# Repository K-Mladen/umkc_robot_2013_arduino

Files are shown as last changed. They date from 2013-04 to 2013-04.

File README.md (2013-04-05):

umkc_robot_2013_arduino
=======================

This is the Arduino code for the UMKC Robotics Team for the 2013 IEEE R5 
competition.

Flash this to the Arduino using the Arduino IDE version 0023. (NOT any 
version above 1.0)

Include the ros_lib directory in Arduino's libraries, either in it's own 
directory\libraries, or under your Documents\Arduino\libraries

Wiring diagram included in PDF and FZZ (Fritzing) format. Frizing is available
by going to www.fritzing.org.

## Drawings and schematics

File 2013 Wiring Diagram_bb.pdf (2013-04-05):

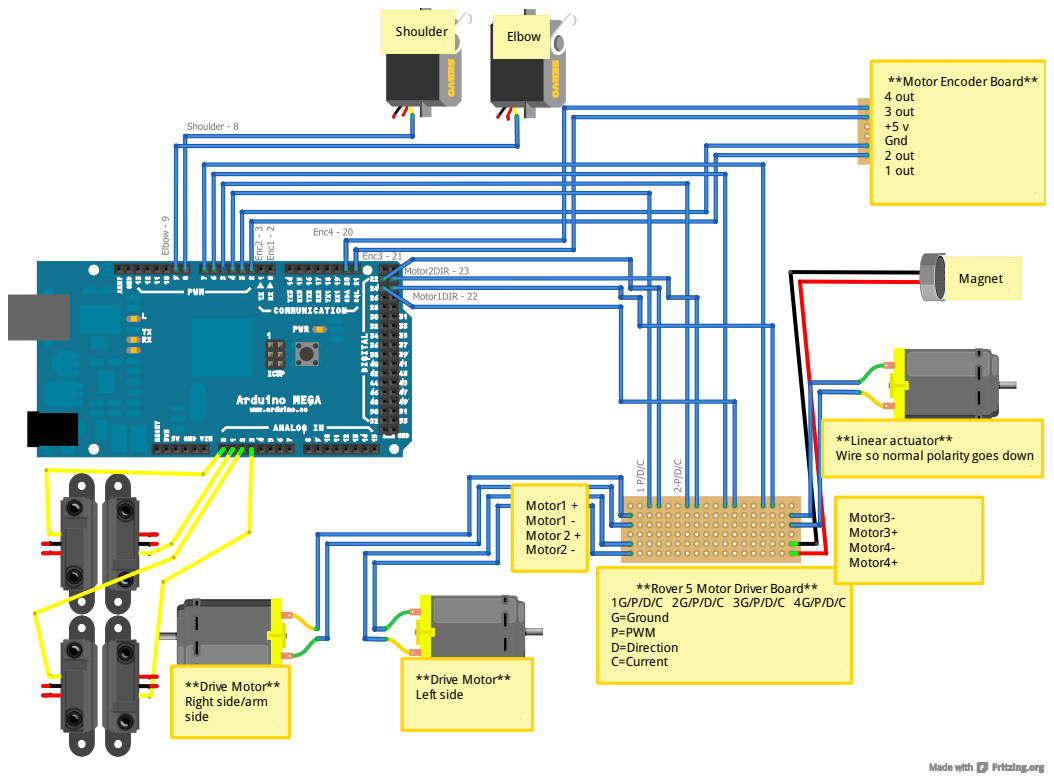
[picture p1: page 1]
**Motor Encoder Board** 4 out 3 out +5 v Gnd 2 out 1 out; **Rover 5 Motor Driver Board** 1G/P/D/C 2G/P/D/C 3G/P/D/C 4G/P/D/C G=Ground P=PWM D=Direction C=Current; Motor1 + Motor1 - Motor 2 + Motor2 -; Motor3- Motor3+ Motor4- Motor4+; **Drive Motor** Left side; Elbow; Shoulder; Magnet

**Linear actuator**
Wire so normal polarity goes down

**Drive Motor**
Right side/arm
side

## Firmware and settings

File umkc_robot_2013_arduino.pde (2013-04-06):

/***************************************
 * Main Arduino robot functions
 * UMKC Robot Team 2013
 * Sarah Withee, Eric Gonzalez
 * Created: February 16, 2013
 * Modified: April 5, 2013
 ***************************************/

/***************************************
 * Pin outs
 ***************************************/
// Digital pins
const byte motor1Dir = 	22;
const byte motor2Dir = 	23;
const byte motor3Dir = 	24;
const byte motor4Dir = 	25;
//const byte LCDOut = 	18;

// PWM pins
const byte motor1PWM = 	4;
const byte motor2PWM = 	5;
const byte motor3PWM = 	6;
const byte motor4PWM = 	7;

// Analog pins
// removed as they're not connected


/***************************************
 * includes
 ***************************************/
#include <Servo.h>
#include <ros.h>
#include <std_msgs/Int16.h>
#include "LCDScreen.h"
#include "Motors.h"
#include "IRSensors.h"


/***************************************
 * ROS variables
 ***************************************/
ros::NodeHandle nh;

// Listen to motherboard
void lmotor_catch(const std_msgs::Int16& message);    
void rmotor_catch(const std_msgs::Int16& message);    
ros::Subscriber<std_msgs::Int16> listenLMotor("lmotor_cmd", &lmotor_catch);
ros::Subscriber<std_msgs::Int16> listenRMotor("rmotor_cmd", &rmotor_catch);

// Talk to motherboard
std_msgs::Int16 lEnc;
std_msgs::Int16 rEnc;
ros::Publisher pubLWheel("lwheel", &lEnc);
ros::Publisher pubRWheel("rwheel", &rEnc);

/*
void debug(String line1, String line2) {
	lcd.print(line1, 1);
	lcd.print(line2, 2);
} */
/***************************************
 * Other variables
 ***************************************/
// Objects
static Motors motors;
LCDScreen lcd;
Servo shoulder;
Servo elbow;
IRSensor ir1;
// Variables
int lmotor_speed = 0;
int rmotor_speed = 0;
boolean updatedSpeed = false;
boolean updatedEncoder = false;
boolean direction = true;
int encoder1;
int encoder2;
int encoder3;
int encoder4;
int currentTime;
int oldTime;

boolean hasStarted = false;

/***************************************
 * ROS Motor message catching
 ***************************************/
void lmotor_catch(const std_msgs::Int16& message) {    
	//debug("main:","lmotor_catch");
	// Caught motor speed message, save and set to future update
	lmotor_speed = message.data;
	updatedSpeed = true;
}  
void rmotor_catch(const std_msgs::Int16& message) {    
	//debug("main:","Rmotor_catch");
	// Caught motor speed message, save and set to future update
	rmotor_speed = message.data;
	updatedSpeed = true;
}

/***************************************
 * Arduino set
 ***************************************/
void setup() {
	// Has to stay at 19200 for screen to function correctly
	Serial1.begin(19200);   // LCD
	lcd.init();
	lcd.clear();
	lcd.backlight(true);
	lcd.on(true);
	lcd.print("Booting, please wait...");


	shoulder.attach(8);
	elbow.attach(9);
	delay(50);
	shoulder.write(170);
	elbow.write(50);


	encoder1 = 0;
	encoder2 = 0;
	encoder3 = 0;
	encoder4 = 0;
	
//	attachInterrupt(0, enc1Interrupt, RISING);
	attachInterrupt(1, enc2Interrupt, RISING);
	attachInterrupt(2, enc3Interrupt, RISING);
//	attachInterrupt(3, enc4Interrupt, RISING);
	// Start at 0, in case any of the interrupts increase it immediately
	encoder1 = 0;
	encoder2 = 0;
	encoder3 = 0;
	encoder4 = 0;
	
	ir1.init(2);
	
//	debug("main:","init_node");
	nh.initNode();
	nh.subscribe(listenLMotor);
	nh.subscribe(listenRMotor);
	nh.advertise(pubRWheel);
	nh.advertise(pubLWheel);
	//debug("main:","nh complete");
	
	lcd.clear();
	lcd.print("Arduino/base OK Go:Flip switch");
}

/***************************************
 * Arduino loop
 ***************************************/
void loop() {
	if(digitalRead(50) == HIGH) {
		if(!hasStarted) {
		    // print started msg
			lcd.clear();
		    lcd.print("Driving...");
		    hasStarted = true;
		    
			//                            |
			// Raise arm at start         |
			// Raise until it's........  \/  inches
			//motors.armStartUp();
			//while(ir1.getDistanceIn() < 3.5) {
			//	delay(1);
			//}
			//motors.armStop();									    
		}	
		
		// Check with ROS to find any new messages
		//debug("main:","nh.initNode()");
		nh.spinOnce();
		
		//debug("loop:", "send Enccoders") 
		if(updatedSpeed) {
			motors.setLMotorSpeed(lmotor_speed);
			motors.setRMotorSpeed(rmotor_speed);
			updatedSpeed = false;
		}
		
		//debug("loop:","Rainbow skittles!");
		currentTime = millis();
		if(currentTime - oldTime > 50) {
		//if(updatedEncoder) {
			lEnc.data = encoder2;
			rEnc.data = encoder3;
			pubLWheel.publish( &lEnc );
			pubRWheel.publish( &rEnc );
			updatedEncoder = false;
			oldTime = millis();
		}
	}
}

void enc1Interrupt() {
	if(motors.getLMotorDir())
		encoder1++;
	else
		encoder1--;
}

void enc2Interrupt() {
	if(motors.getLMotorDir())
		encoder2++;
	else
		encoder2--;
}

void enc3Interrupt() {
	if(motors.getRMotorDir())
		encoder3++;
	else
		encoder3--;
}

void enc4Interrupt() {
	if(motors.getLMotorDir())
		encoder4++;
	else
		encoder4--;
}

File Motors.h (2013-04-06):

/***************************************
 * Arduino motor controller code
 * UMKC Robot Team 2013
 * Sarah Withee
 * Created: February 16, 2013
 * Modified: April 6, 2013
 ***************************************/

// Arduino stuff
#ifndef Motors_h
#define Motors_h
// include types & constants of Wiring core API
#include "WProgram.h"

class Motors { 
private:
	// Keep some vars to help keep track of some stuff
	boolean lDir, rDir;   // default forward;
	int lSpeed, rSpeed;
public:
	// Setup pin outs and stuff
	Motors() {
		// Speed controls
		pinMode(motor1PWM, OUTPUT);
		pinMode(motor2PWM, OUTPUT);
		pinMode(motor3PWM, OUTPUT);
		pinMode(motor4PWM, OUTPUT);
		// Direction control
		pinMode(motor1Dir, OUTPUT);
		pinMode(motor2Dir, OUTPUT);
		pinMode(motor3Dir, OUTPUT);
		pinMode(motor4Dir, OUTPUT);
		// Current goes up/down (?) if resistance to motor goes up
		//pinMode(motor1Cur, INPUT);
		//pinMode(motor2Cur, INPUT);
		
		lDir = true;
		rDir = true;
		lSpeed = 0;
		rSpeed = 0;
	
	}

        void setLMotorSpeed(int speed) {
		// Left motor is connected to controller motor 2
		if(speed > 255) speed = 255;
		if(speed < -255) speed = -255;
		if(speed >= 0) {
			digitalWrite(motor2Dir, HIGH);
			//direction = true;
			lDir = true;
		}
		else {
			digitalWrite(motor2Dir, LOW);
			//direction = false;
			lDir = false;
		}
		lSpeed = abs(speed);
		analogWrite(motor2PWM, lSpeed);
        }
        
        void setRMotorSpeed(int speed) {
		// Right motor is connected to controller motor 1
			if(speed >= 0) {
				digitalWrite(motor1Dir, HIGH);
				//direction = true;
				rDir = true;
			}
			else {
				digitalWrite(motor1Dir, LOW);
				//direction = false;
				rDir = false;
			}
			rSpeed = abs(speed);
			analogWrite(motor1PWM, rSpeed);
        }

        void armStartDown(int speed = 255) {
			// Set to motor 3
			digitalWrite(motor3Dir, LOW);
			analogWrite(motor3PWM, speed);
        }
        void armStartUp(int speed = 255) {
			// Set to motor 3
			digitalWrite(motor3Dir, HIGH);
			analogWrite(motor3PWM, speed);
        }
        void armStop() {
			digitalWrite(motor3Dir, HIGH);
			analogWrite(motor3PWM, 0);
        }
        void magnet(boolean setOn) {
		// Set to motor 4
		digitalWrite(motor4Dir, HIGH);
		if(setOn)
			analogWrite(motor4PWM, 255);
		else
			analogWrite(motor4PWM, 0);
        }

        boolean getLMotorDir() {
          return lDir;
        }
        boolean getRMotorDir() {
          return rDir;
        }
};

#endif

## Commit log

2013-03-26 Code from 2/16/2013
    Libraries for IR sensor, LCD screen, and motor drive functions.
    Communicates with ROS and works with a forward or stop command.
    [2013 Wiring Diagram.fzz]
2013-03-26 Renamed PDE file to match new repo name
    Renamed to make Arduino happy
    From MotorTestSarah.pde to umkc_robot_2013_arduino.pde
2013-04-03 Several changes (see comments)
    IR Sensors:
    - Updated IR Sensor code to work with newer Arduino IDE (v1.0 or newer)
    LCD screen:
    - Updated LCD code to work with newer Arduino IDE (v1.0 or newer)
    Main:
    - Renamed main file to match GitHub name and sketch name in Arduino
    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
2013-04-05 Driving functions working correctly
    Encoders:
    - Removed encoder.h include
    - Moved functions to main file, only way to get interrupts to work in
    friendly way
    Motors:
    - Added commands to set individual motor speeds
    - Added commands to get motor directions
    Wiring diagram:
    - Added magnet, arm motor, and IR sensor wiring
    [2013 Wiring Diagram.fzz]
2013-04-05 Encoder functions working correctly (in theory)
    Encoder publishers are being received by ROS. Encoders 1 and 4 seem to
    be not working, so using 2 and 3.
    [Motors.h, umkc_robot_2013_arduino.pde]
2013-04-06 Added LCD code and whatever Andrew changed
    LCD displays test message, with minor mods can print out any message
    Andrew changed stuff (baud rate?) so that's in here too.
2013-04-06 Locked servos, removed old files
    - Servos now stay in place so they can drive around
    - Removed encoders.h (code moved to main)
    - Removed Wall.h (no longer using message type)
    - Andrew changed baud rate back
    [Motors.h, umkc_robot_2013_arduino.pde]
2013-04-06 FINAL: Round 2 code
    Code that was applied to robot for round 2.
    - Included IR sensor header, but not used, therefore code is commented
    out.
    - If motor values are x < -255 or x > 255, it's rounded down to (+/-)
    255
    - Improved LCD code, actually prints what it's doing.
    - Board waits for "go" switch before going
    - Fixed IR sensor class so pin is attached to object
    [Motors.h, umkc_robot_2013_arduino.pde]
